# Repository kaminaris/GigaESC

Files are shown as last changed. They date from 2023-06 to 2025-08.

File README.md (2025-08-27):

# GigaESC - 40s 400A

GigaESC - Based upon the VESC®*-Project VESC is a registered TM, owned by Benjamin Vedder




* Modular design
* Logic board
* Separate Power Stage (Mosfet) board
* 40s capable
* Up to 188V (Mosfets and caps up to 200V)
* Up to 300A (depending on choice of mosfets)
* Hall sensor current measurement or low side shunts
* Built in IMU - LSM6DS3TR-C
* Optional Hardware current protection
* Designed for easy manufacturing at JLCPcb (KiCad Fabrication Toolkit)

Licensed under [Creative Commons Attribution-NonCommercial-ShareAlike 4.0 International License](https://creativecommons.org/licenses/by-nc-sa/4.0/legalcode.en)


# ⚠️Please do not order before contacting me on discord️⚠️

https://discord.gg/embedded

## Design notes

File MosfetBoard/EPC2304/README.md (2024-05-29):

# GigaESC - EPC2304

---

# ⚠️Please do not order before contacting me on discord️⚠️

this is a very hard board to solder requires:

- Good knowledge of microsoldering
- **A microscope**
- Hot air capable of reaching 450°C
- A very thin soldering iron tip
- An oscilloscope

## GaN Soldering procedure

Use 60/40 solder from a reputable source. Trying to use lead-free solder by hand will be extremely difficult. Using poor-quality products will also result in failure, and this applies to flux as well.

This board has 4 layers, so it can absorb a lot of heat. Using high-quality solder is essential because the board is very sensitive to cold joints.

Having a good soldering iron is crucial and can make the difference between success and failure.

To solder GaN mosfets i strongly recommend using soldering paste instead, everything else can be done with wire tin.

1. Apply solder paste with flux on the footprint.
2. Position the GaN mosfet in place.
3. Use hot air until the solder melts and the GaN device is securely in place, applying gentle pressure to ensure proper contact.
4. Remove any excess solder with a soldering iron.
5. Allow the solder to cool down.

**[Repeat]**

1. Heat the solder joint again with hot air.
2. Apply flux.
3. Use tweezers to gently swirl the MOSFET, ensuring each pad has an equal amount of solder.
4. Reposition the MOSFET properly.
5. Allow the solder to cool down.

**[Repeat until the GaN mosfet self-aligns perfectly.]**

**⚠️While doing soldering procedure, make sure there are no microblobs of solder underneath mosfets.**
This may take a couple of tries to get it right.

## Testing procedure

1. Check with a multimeter the following parameters:
    - Resistance between + and - terminals: Should be very high, nearly open loop.
    - Resistance between each phase to ground: Should be greater than 40 kOhms.
    - Resistance between each phase to VBat+: Should be in the megaohms range.
    - Phase comparison: Each phase should have similar resistance readings to the others.
    - Gate connection check: Ensure each gate connects to the main PL and PH lines (this can be verified from the top of the PCB).
2. If electrically everything seems fine, connect to the main board and turn on the VESC:
    - Error code check: If any error code appears, there may be an issue, most commonly cold joints.
    - Current offset measurement:
        - Measure current offsets before doing anything with the VESC. 
        - They should all be within +/-10 LSB and around 2070
         
3. Connect the motor and measure its RL properties:
    - If you observe any abnormal values, such as very high inductance:
       - Check and fix any cold joints.
       - Use a multimeter to ensure each current sensor at idle is outputting about 1.65V.
       - Ensure each current sensor is receiving 5V.
4. Once any initial problems are resolved:
    - Set the current to the lowest possible value in FOC -> General and perform a full detection until all parameters are green and appear reasonable:
    
    - If you have another VESC, compare results with it. It will depend on motor itself so do not compare them to mine.
    - Perform a short double pulse test, for example: double_pulse 100 10 5 10. Confirm both edges look okay and are not overshooting.
    - Perform the motor detection.

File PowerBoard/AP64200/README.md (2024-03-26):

# Power Supply AP64200

## ⚠ Not working - Do not use ⚠

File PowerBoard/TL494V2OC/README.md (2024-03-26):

# Power Supply TL494 V2

Version without power switch

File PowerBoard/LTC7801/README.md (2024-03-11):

# Power Supply LTC7801

## ⚠ Not working - Do not use ⚠

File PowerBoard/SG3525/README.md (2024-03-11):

# Power Supply SG3525

## ⚠ Not working - Do not use ⚠

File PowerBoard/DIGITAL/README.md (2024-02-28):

# Power Supply DIGITAL

## ⚠ Not working - Do not use ⚠

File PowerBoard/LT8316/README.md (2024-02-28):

# Power Supply LT8316

## ⚠ Not working - Do not use ⚠

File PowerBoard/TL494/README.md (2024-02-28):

# Power Supply TL494

Version without power switch

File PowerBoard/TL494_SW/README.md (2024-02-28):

# Power Supply TL494

Version with power switch

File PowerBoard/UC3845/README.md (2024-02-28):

# Power Supply UC3845

## ⚠ Not working - Do not use ⚠

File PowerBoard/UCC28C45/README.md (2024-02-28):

# Power Supply UCC28C45

## ⚠ Not working - Do not use ⚠

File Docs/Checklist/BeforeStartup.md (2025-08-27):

# Things to check before starting up VESC for first time

1. Visual inspection for solder bridges and correct orientation of polarized parts.
2. Check for shorts between power rails:
   - battery + and -
   - motor phases
   - 12V, 5V, and 3.3V rails
3. Check if all drivers capacitors have roughly the same voltage drop.
4. Use a current-limited power supply for initial power-up 1-3A should be enough.

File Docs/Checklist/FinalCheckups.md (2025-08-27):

# Final Checkups for VESC-based ESC

2. Use a thermal camera to check for unexpected hot spots during operation at low power.
3. Verify deadtime settings in firmware/configuration to prevent shoot-through:
    - Connect oscilloscope to high and low gates. Make sure the deadtime is sufficient to prevent overlap.
      
    - Make sure phase voltage does not spike too much
      
4. Double pulse test:
    - Clean the board and ensure no debris or solder balls are present.
    - Connect one probe to phase 1 and another to output of current sensor.
    - `double_pulse 100 10 5 10` - Preface, first on time, off time, second on time
    - gradually increase the voltage and time on for the first pulse looking out for issues
    - Check for double pulses on the high side gate.
      
6. Run foc_openloop_test to verify motor operation:
    - Set the test to a low current (e.g., 5A) and observe motor behavior.
    - Ensure the motor spins smoothly without excessive noise or vibration.
    - Check for any abnormal current spikes or temperature increases.
4. Calibrate current sensors using VESC Tool or relevant software, confirm accurate readings.
7. Review all configuration parameters before full-power operation.

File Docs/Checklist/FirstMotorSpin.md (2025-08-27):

# First Motor Spin Checklist for VESC-based ESC

1. **Use bench power supply with current limit (1-3A).** Confirm board powers up without faults.
2. Connect motor phases to ESC
3. Connect to VESC Tool.
4. Set current limits to low values (e.g., 5-10A) in Motor -> General -> Current Tab.
5. Write motor configuration to ESC.
6. Perform motor detection, make sure it ends up with reasonable values.

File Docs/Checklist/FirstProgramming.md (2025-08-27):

# First Programming Checklist for VESC-based ESC

1. Confirm essential power rails 3.3V are present and stable.
2. Connect the programming header SWD to the microcontroller.
3. Ensure the board is powered via a current-limited supply (1-3A max).
4. Use either black magic probe or ST-Link for programming.
5. Load the appropriate firmware onto the ESC.
6. Connect the ESC to a computer via USB and connect with vesc tool.
7. **DO NOT forget to upload bootloader first if it is not already present.**
8. Monitor for excessive current draw or heating during programming. 
It should be around 0.04A

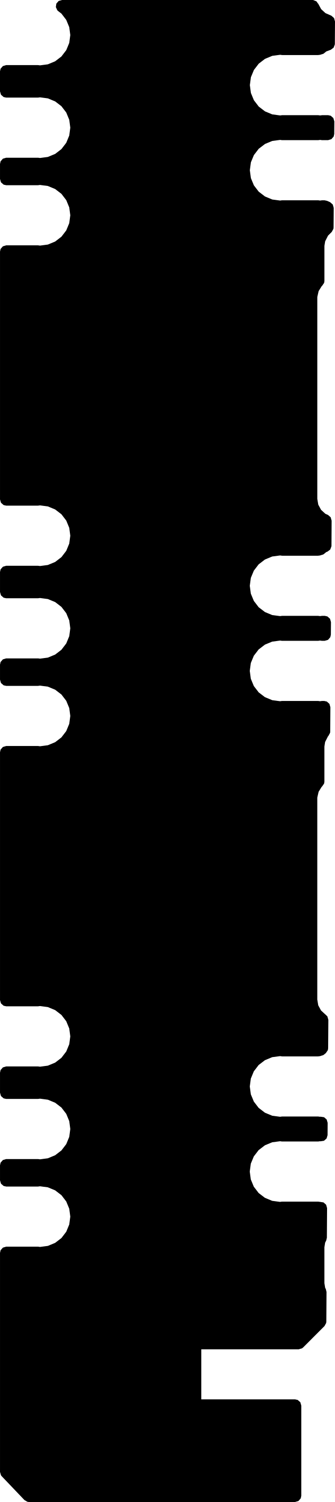
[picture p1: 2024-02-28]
MosfetBoard/EPC2304/bitmap.png

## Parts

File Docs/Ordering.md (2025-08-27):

## Ordering guide

Make sure you have KiCad 7 installed and plugin for kicad "Fabrication Toolkit"

1. Open project you want to edit in Kicad7
2. Open board file (pcbnew)
3. Click the button to export production files



4. New folder will open up with all the files required for jlcpcb
5. Upload gerber.zip on front page
6. Check assembly on the bottom of page, change quantity to 2 (you cannot order just one)



7. Most of the board are top side only with exclusion of power boards.
8. On next page upload appropriate files



9. On next page you will have the opportunity to not place certain components if
   you wish to for example not have certain connectors reducing price of assembly.
   **Each project may have specific assembly guide**
10. Inspect the board on 3d render to make sure all components are placed correctly
11. Proceed to order as usual

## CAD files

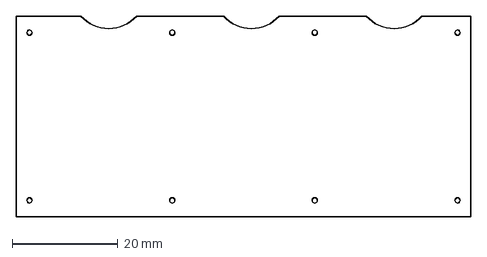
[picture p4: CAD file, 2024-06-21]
3DModels/IHS.dxf
86.0 x 38.0 mm

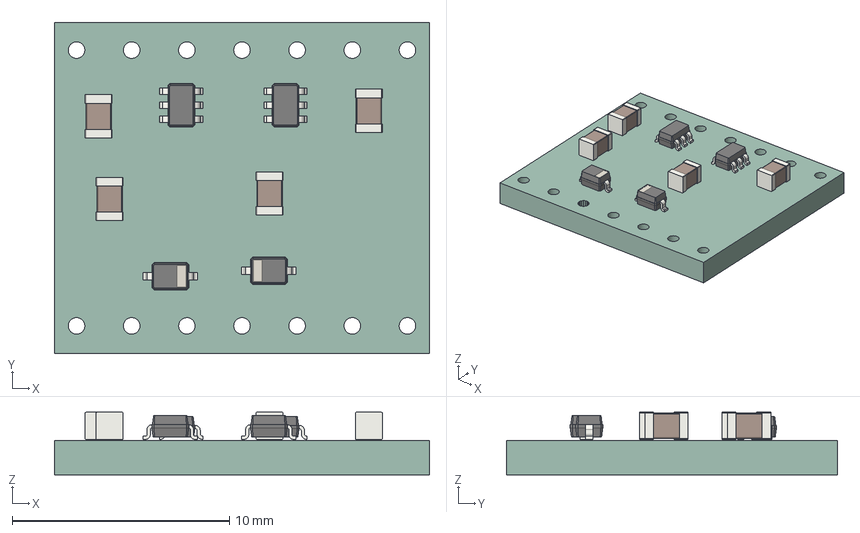
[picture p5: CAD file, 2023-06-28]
HardwareProtection/HardwareProtection.step
17.3 x 15.2 x 2.88 mm
_autosave-HardwareProtection PCB

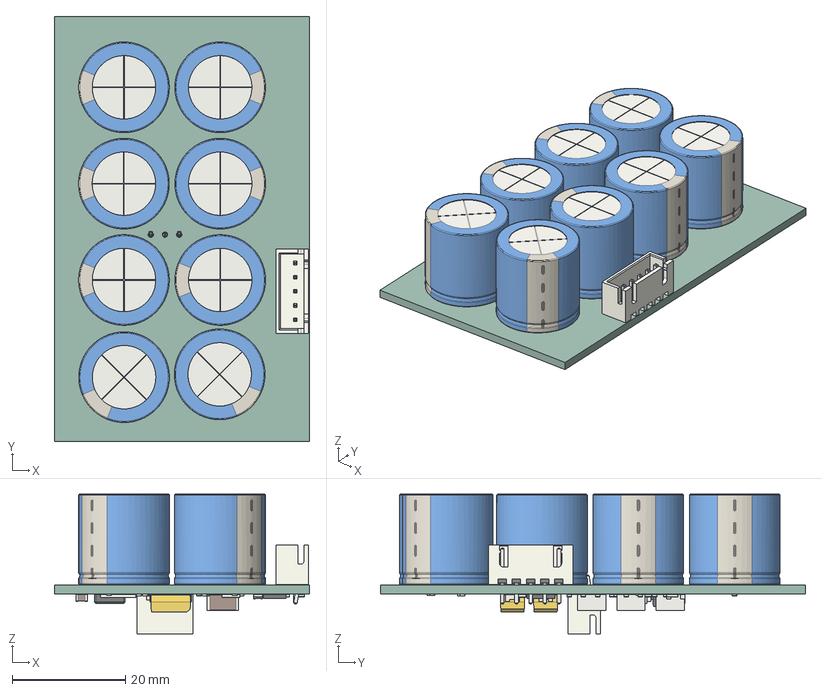
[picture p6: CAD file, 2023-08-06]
PowerBoard/LTC7801/LTC7801.step
45.0 x 75.0 x 24.7 mm
_autosave-LTC7801 PCB

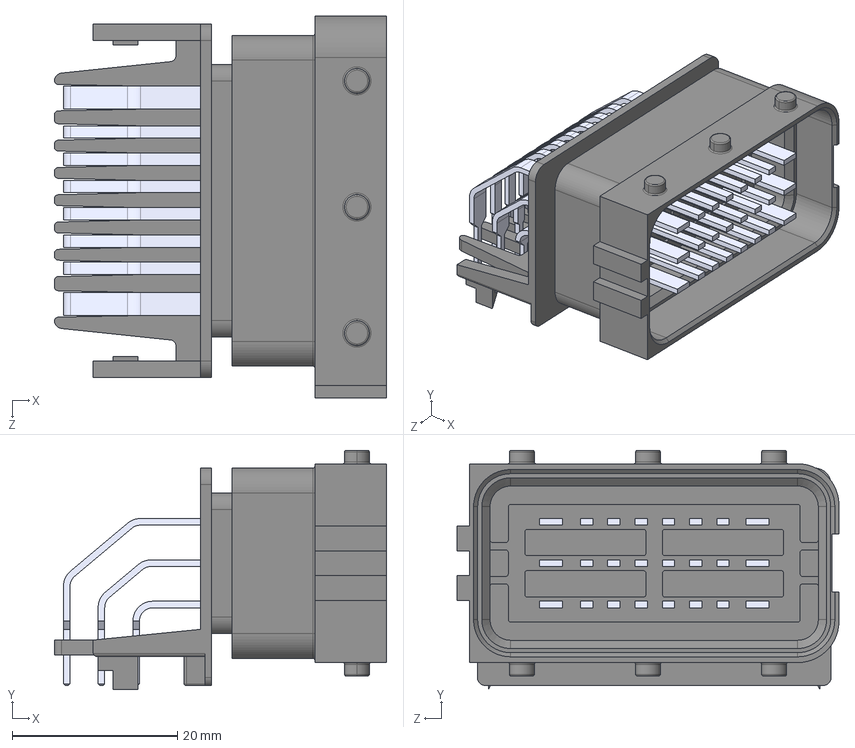
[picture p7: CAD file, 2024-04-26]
Supervisor/3DModels/HCCPHPE24BKA90F.stp
40.2 x 29.0 x 46.2 mm

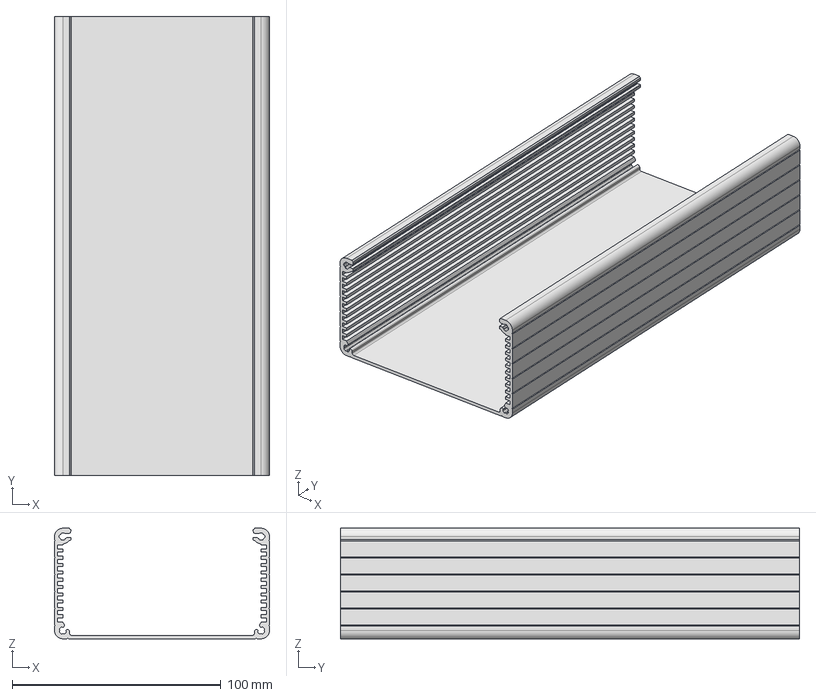
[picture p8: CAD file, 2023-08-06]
WholeDevice/N Extrusion 220mmNoCover.step
103.0 x 220.0 x 53.0 mm

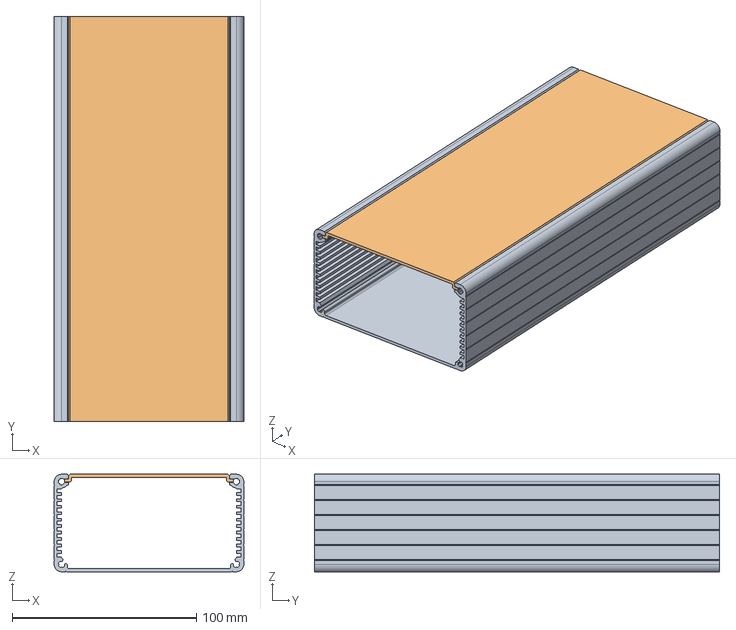
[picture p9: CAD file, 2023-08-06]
WholeDevice/N Extrusion 220mm.stp
103.0 x 220.0 x 53.0 mm
1455N Extrusion 220mm
1455N Cover 220mm

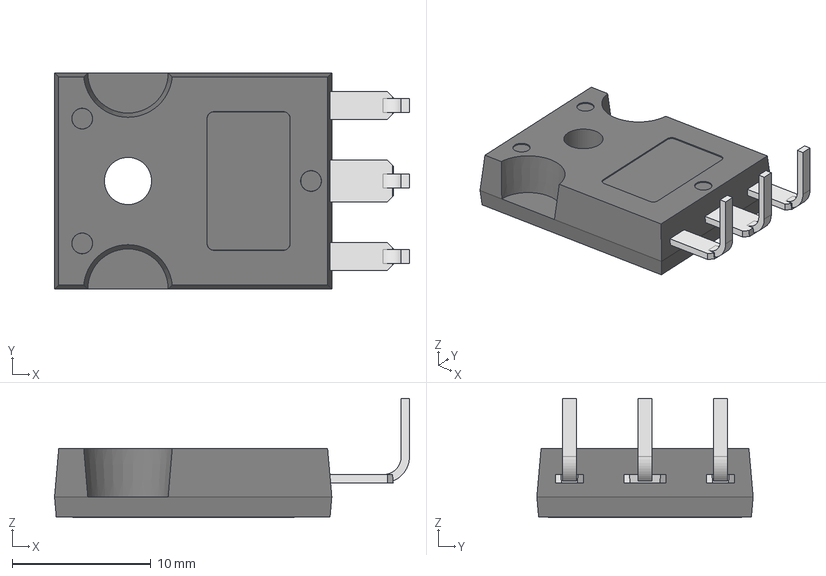
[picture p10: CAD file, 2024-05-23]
3DModels/TO-247_horizontal_back_line.stp
25.6 x 15.6 x 8.60 mm

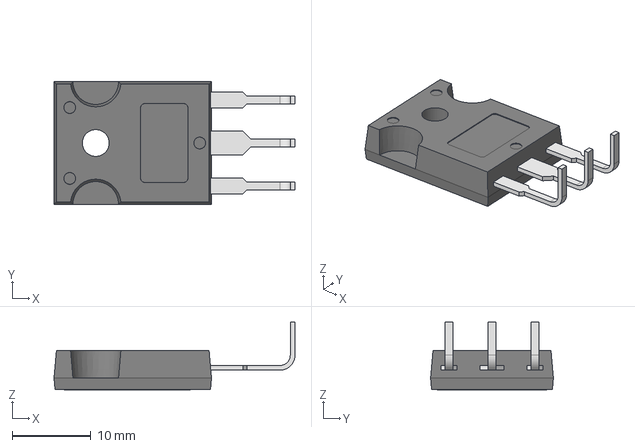
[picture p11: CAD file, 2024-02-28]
3DModels/TO-247_horizontal_back_line-orig.stp
30.6 x 15.6 x 8.60 mm

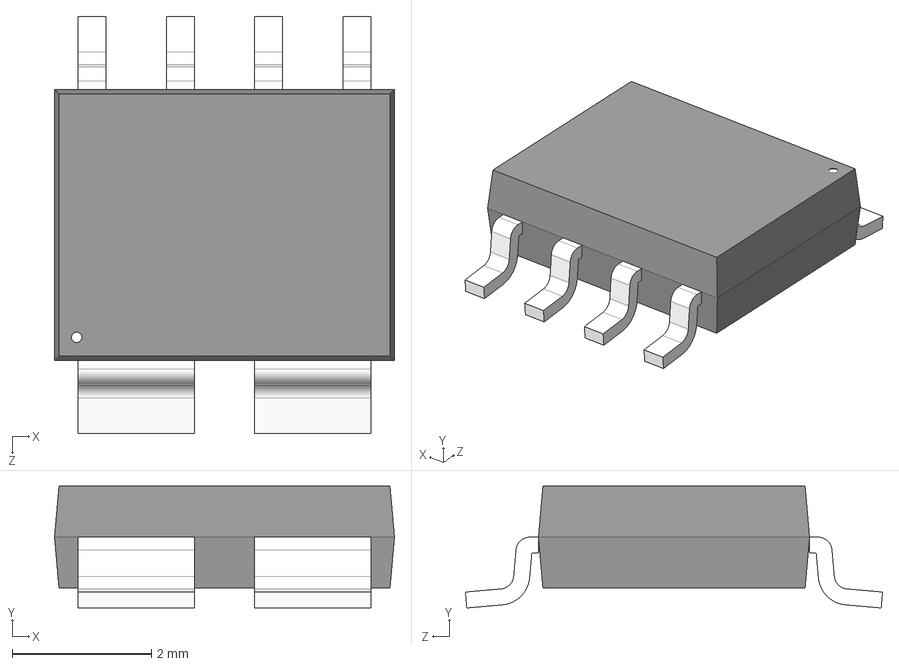
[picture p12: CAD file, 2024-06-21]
3DModels/ACS37030LLZATR-040B3.stp
4.89 x 1.75 x 6.00 mm

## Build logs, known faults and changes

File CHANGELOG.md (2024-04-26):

# Changelog
## V3.3.1
- Supervisor routed
- TL494V2 with over current protection

## V3.3.0
- Updated TL494 V2.1 version
- Initial supervisor

## V3.2.2
- Added TL494 V2 version
- Updated divider resistors with 3-1 ratio.
- Changed JTAG to TagConnect 2030
- Spark switch rework

## V3.2.0
- Moved to KiCad 8
- Updated MCU to bigger package
- Changed inter-board connector to 2x15 pin header
- Added solid mounting screw points
- Updated labels

## V2.1.0
- Added UC3845 power supply board

## V2.0.0
- Connectors changed to JST PH from XH
- Fixed output voltage on ZTP7193Y
- Hardware protection attiny divided for separate digital potentiometers
- Added UART out from attiny for debugging
- Added ESP32-C3 for wireless comm on CANBUS as well as SD card slot for logging
- Added current filter
- Changed analog switches to 7x RS2057XH
- Fixed BRK/Power stage lockout

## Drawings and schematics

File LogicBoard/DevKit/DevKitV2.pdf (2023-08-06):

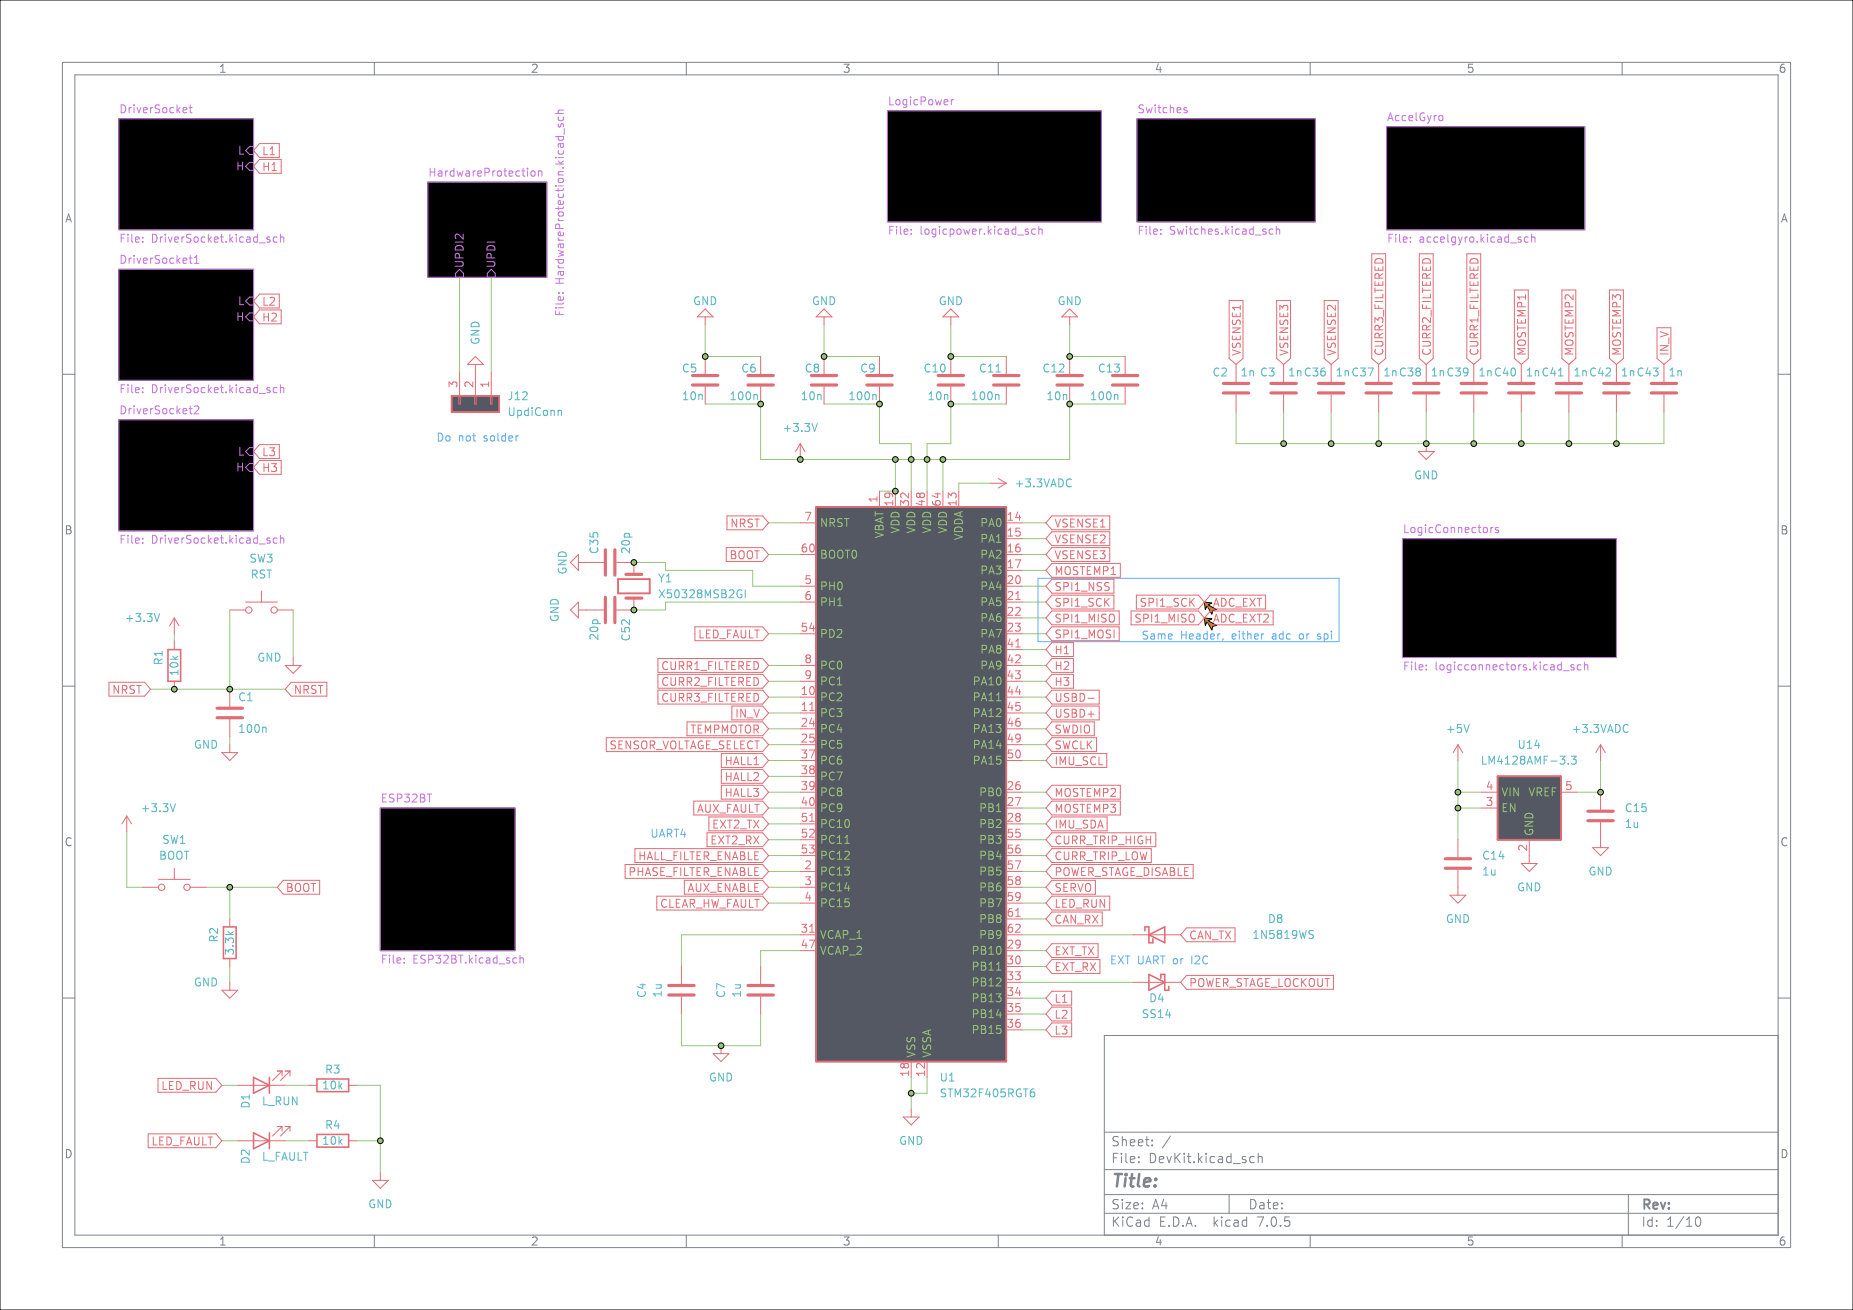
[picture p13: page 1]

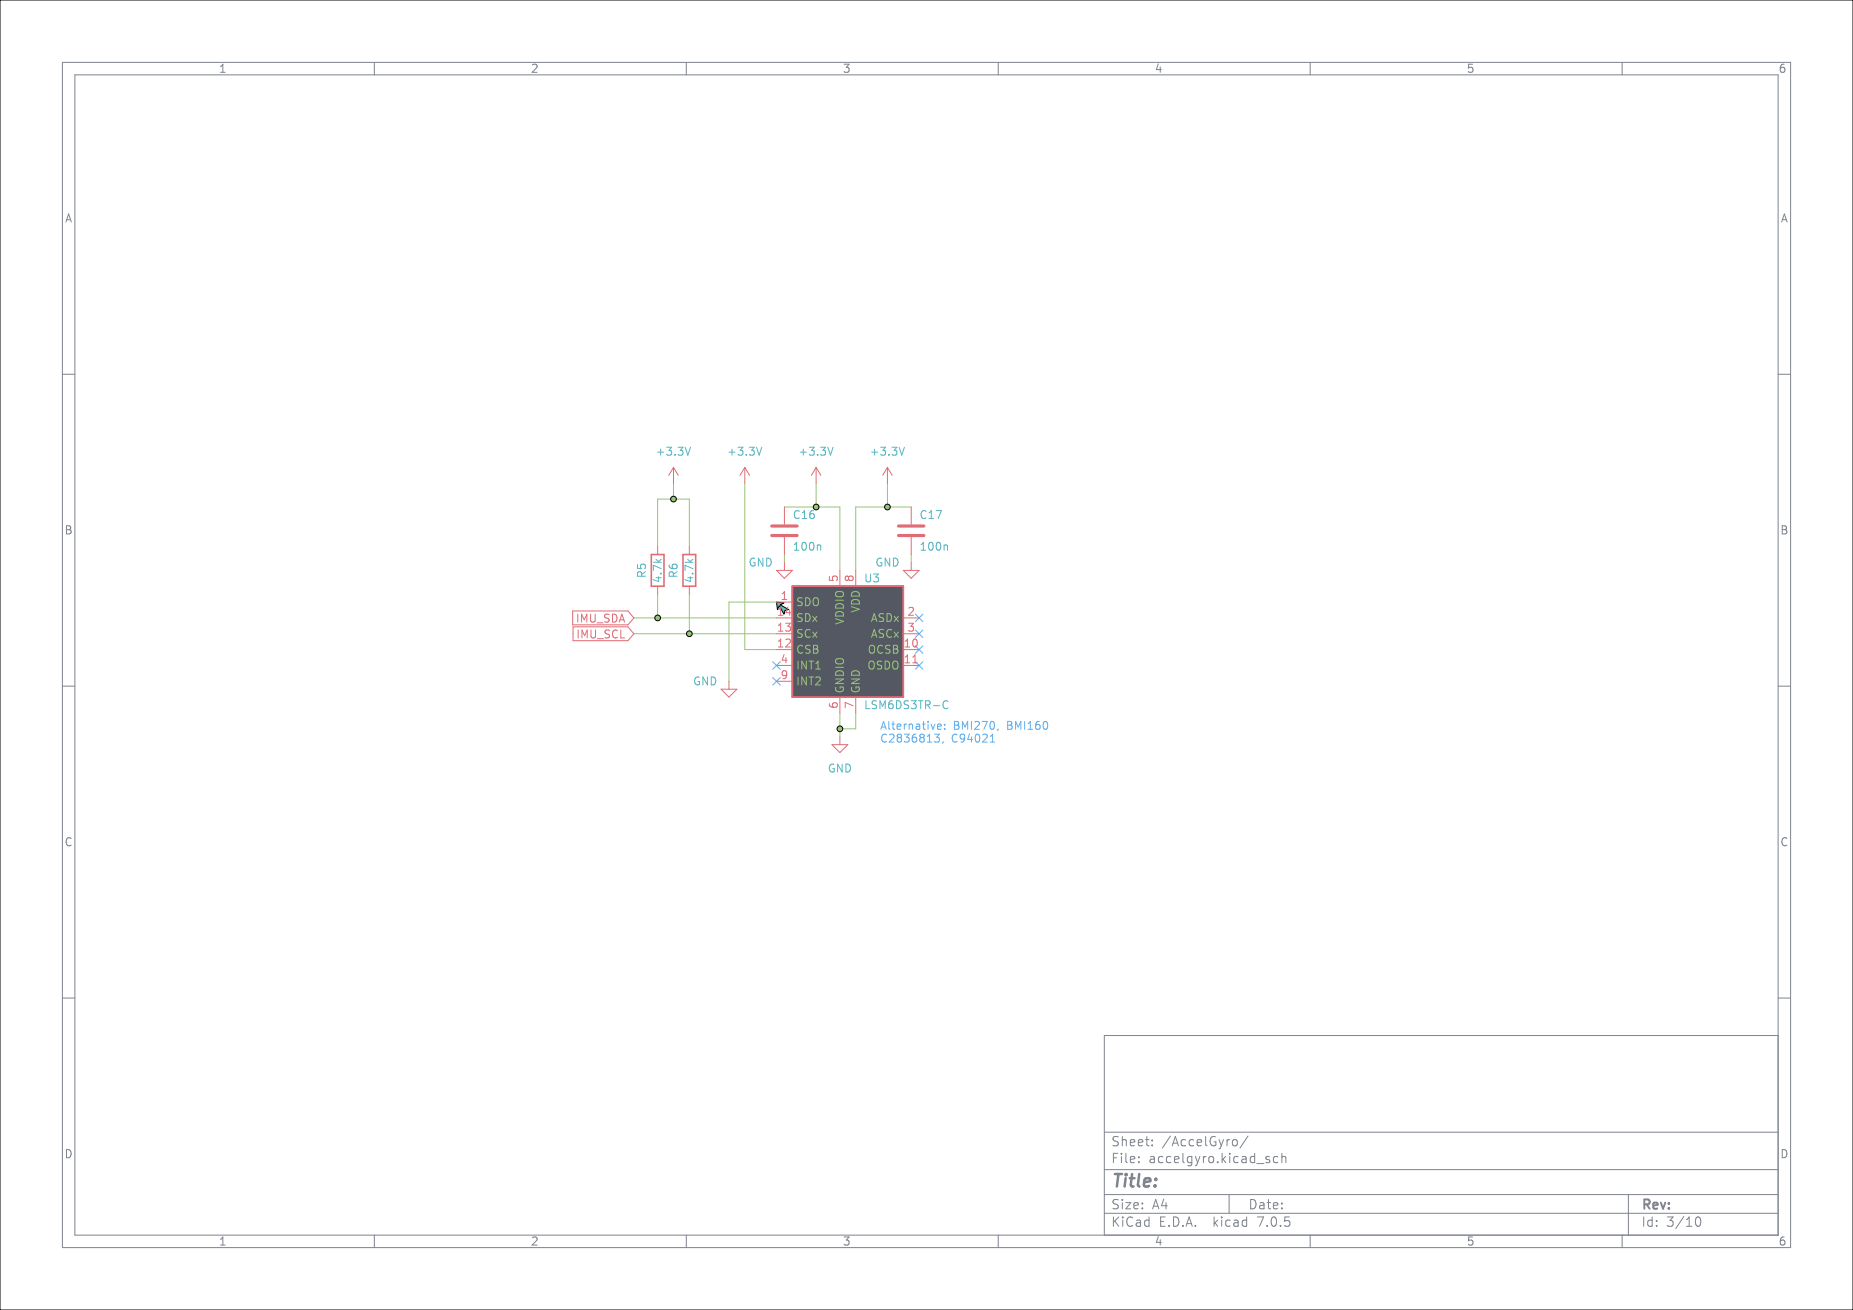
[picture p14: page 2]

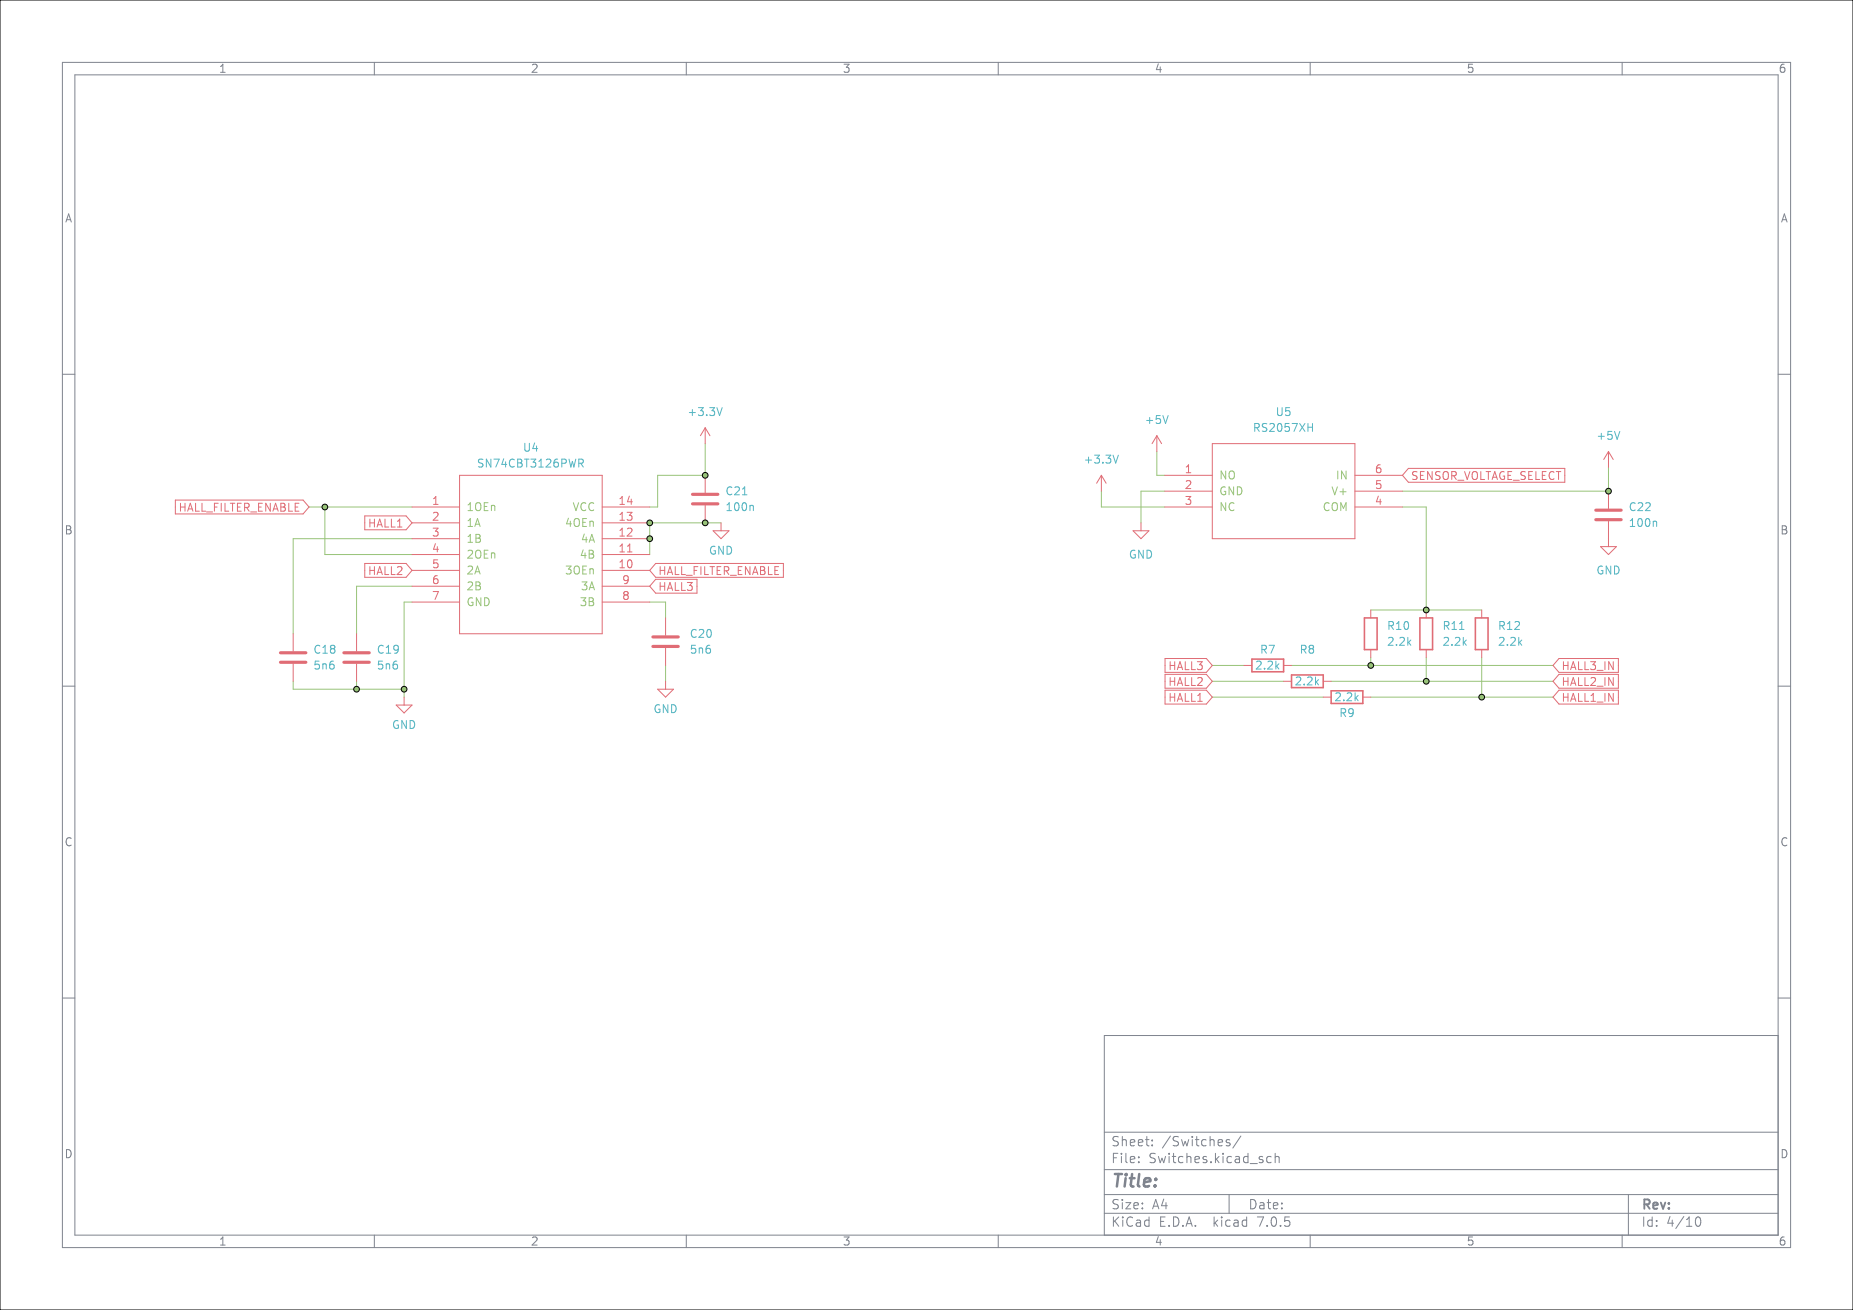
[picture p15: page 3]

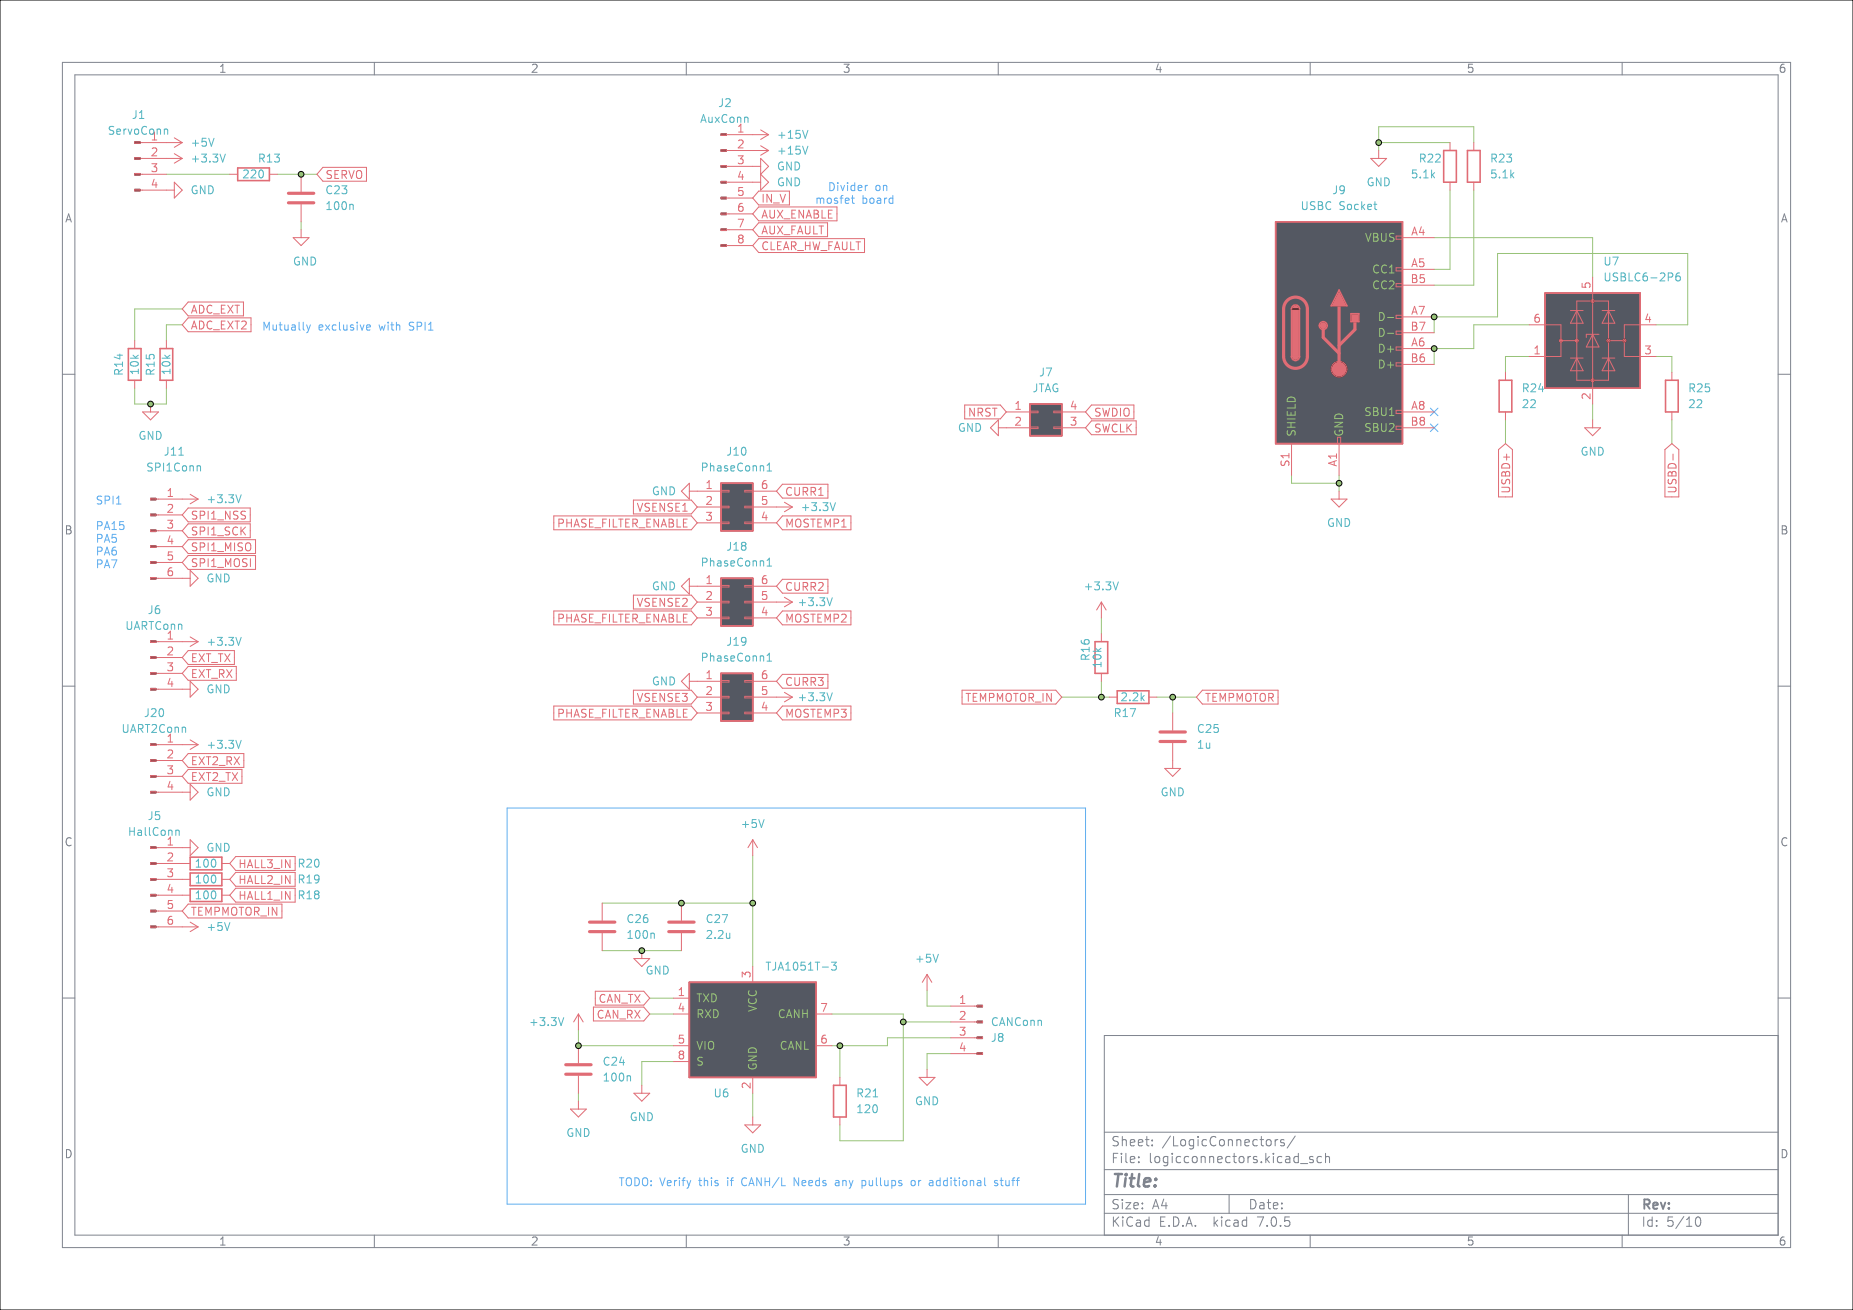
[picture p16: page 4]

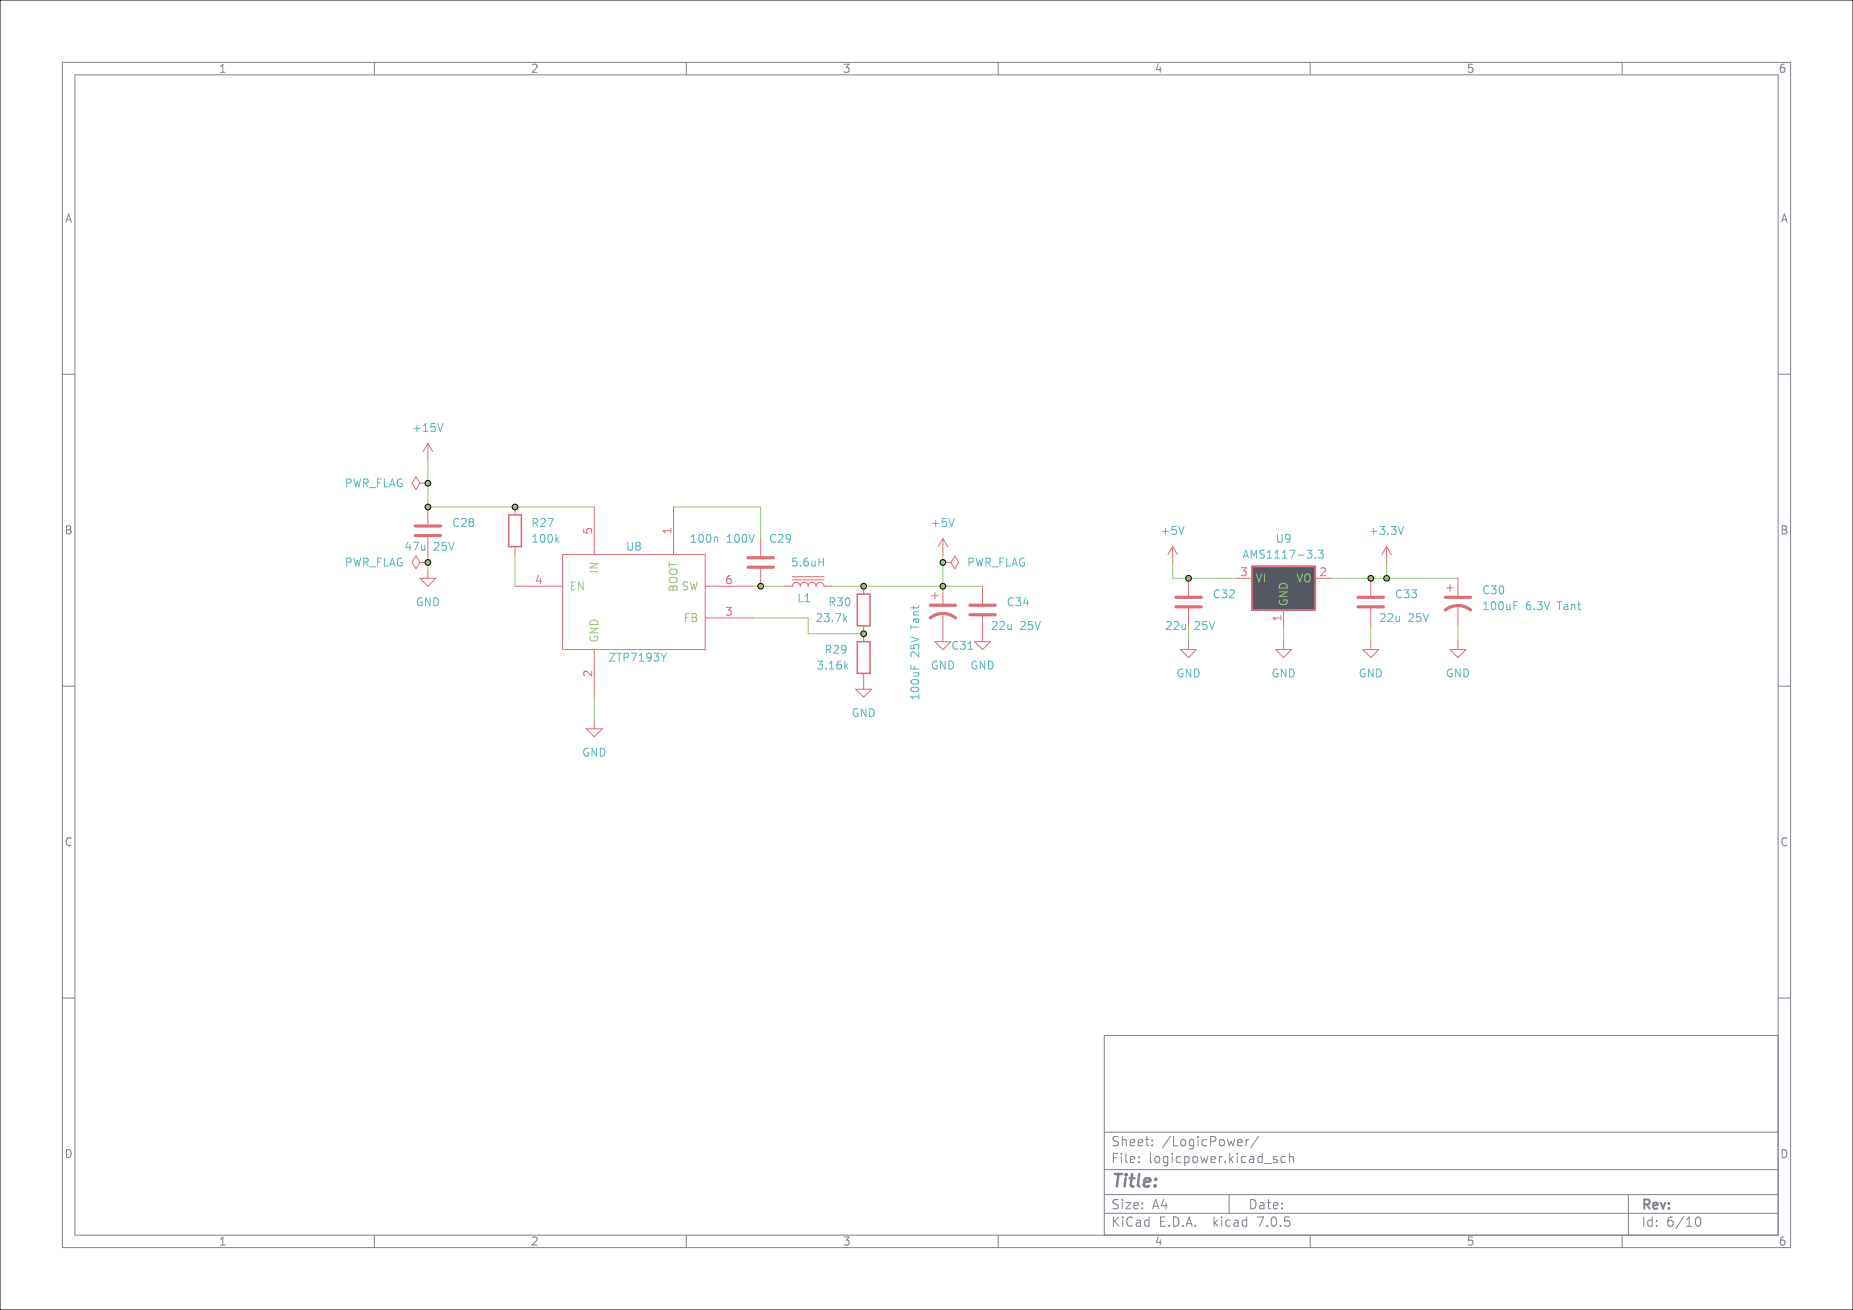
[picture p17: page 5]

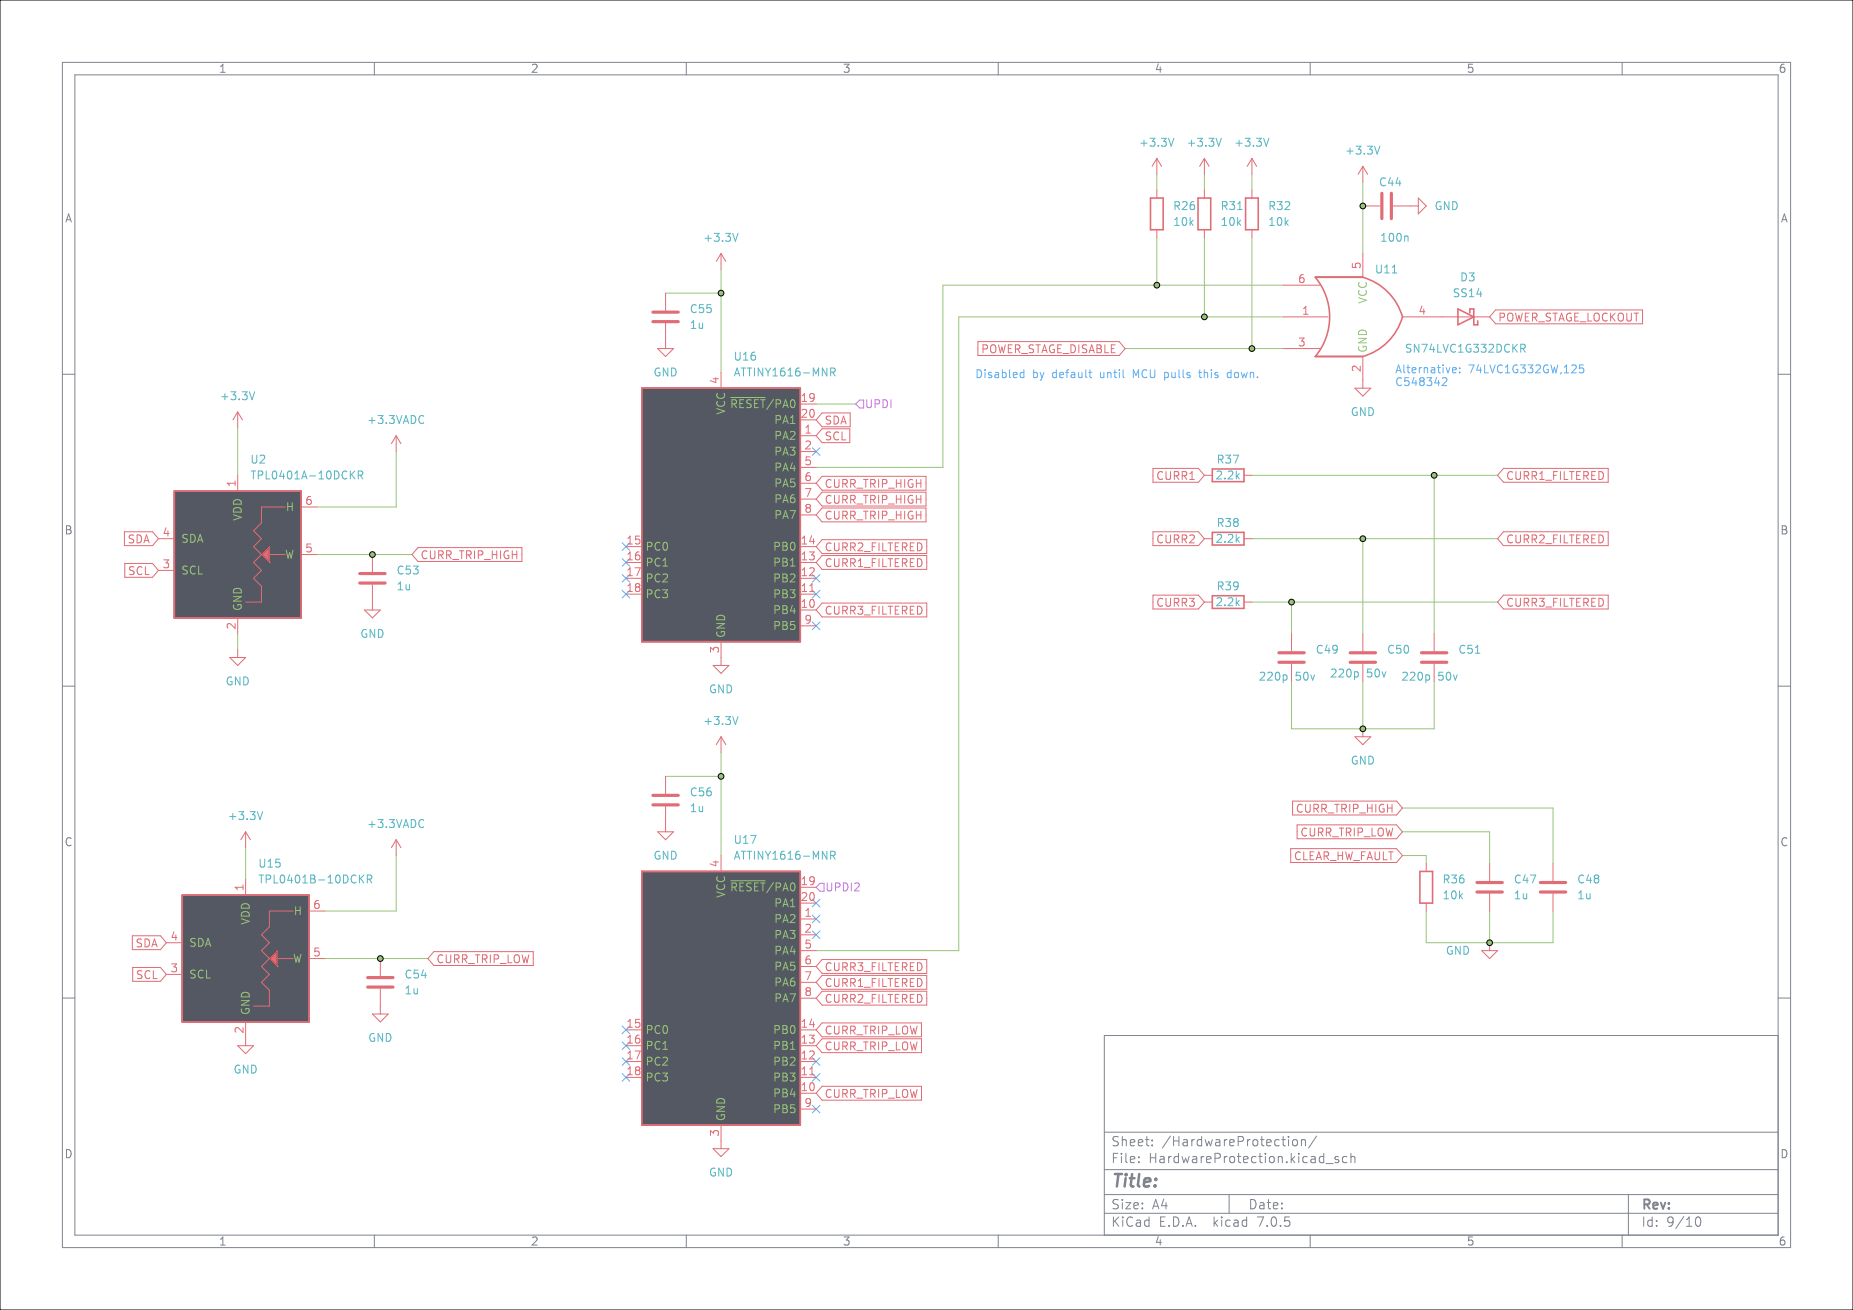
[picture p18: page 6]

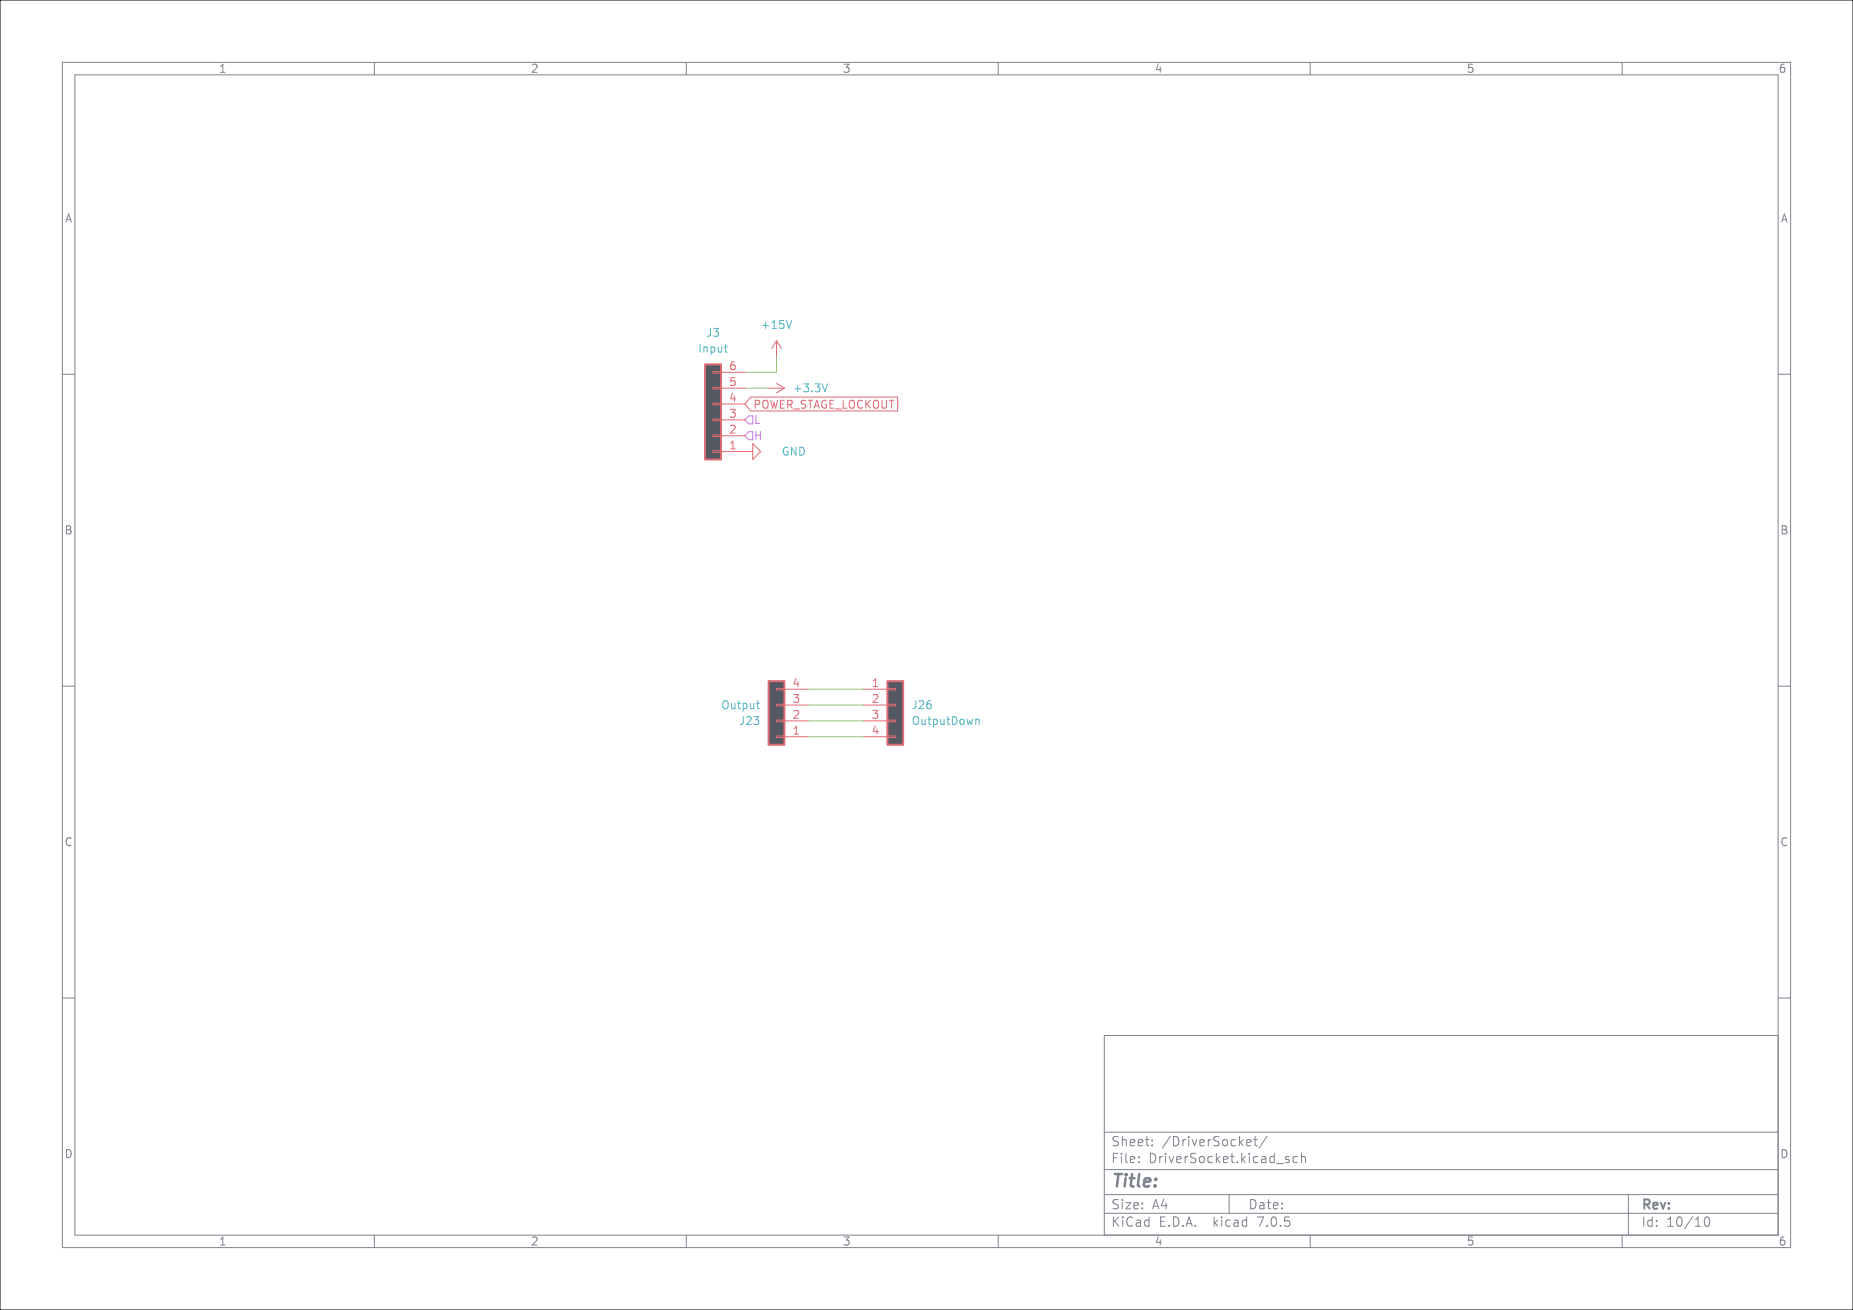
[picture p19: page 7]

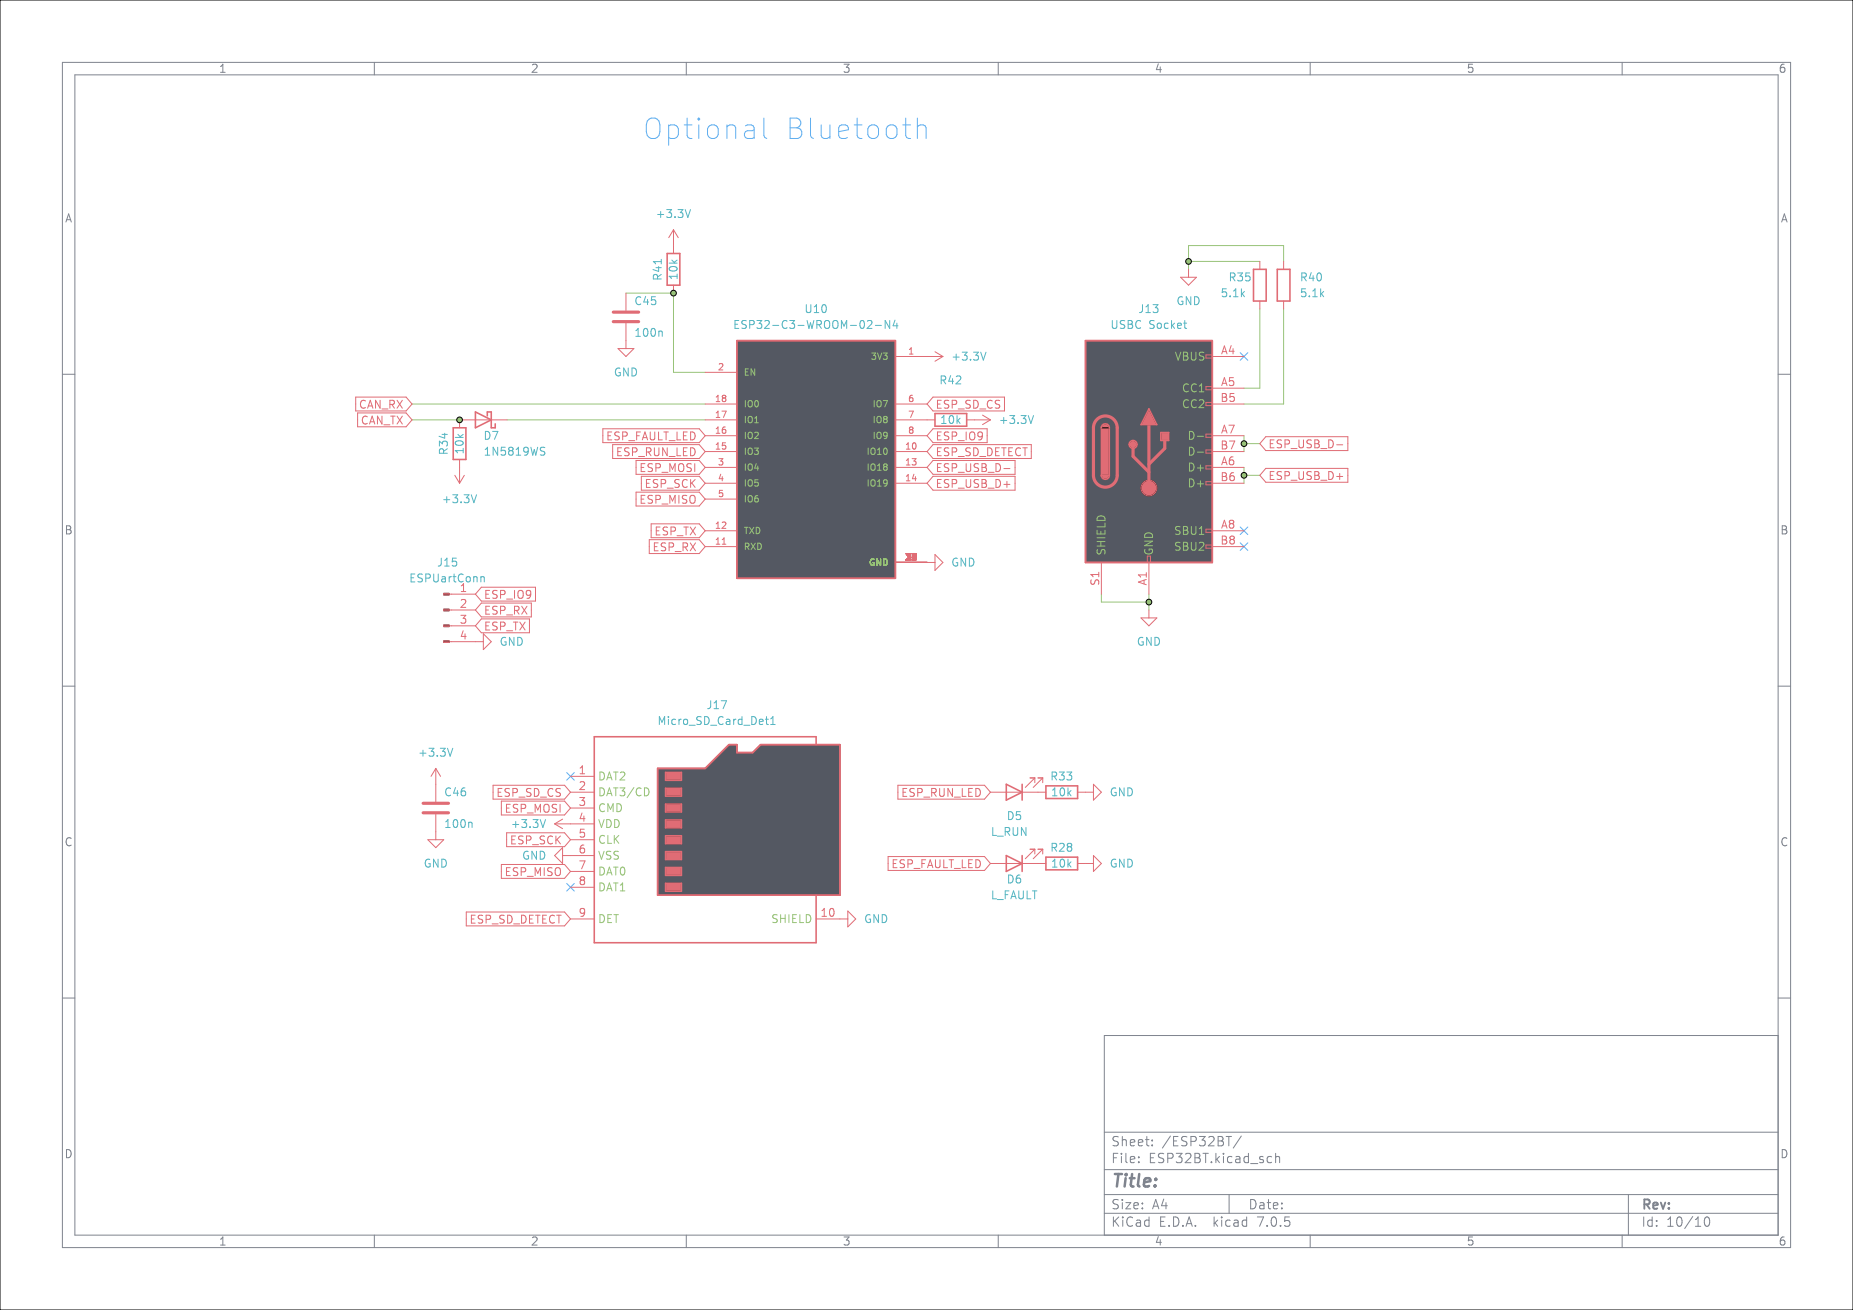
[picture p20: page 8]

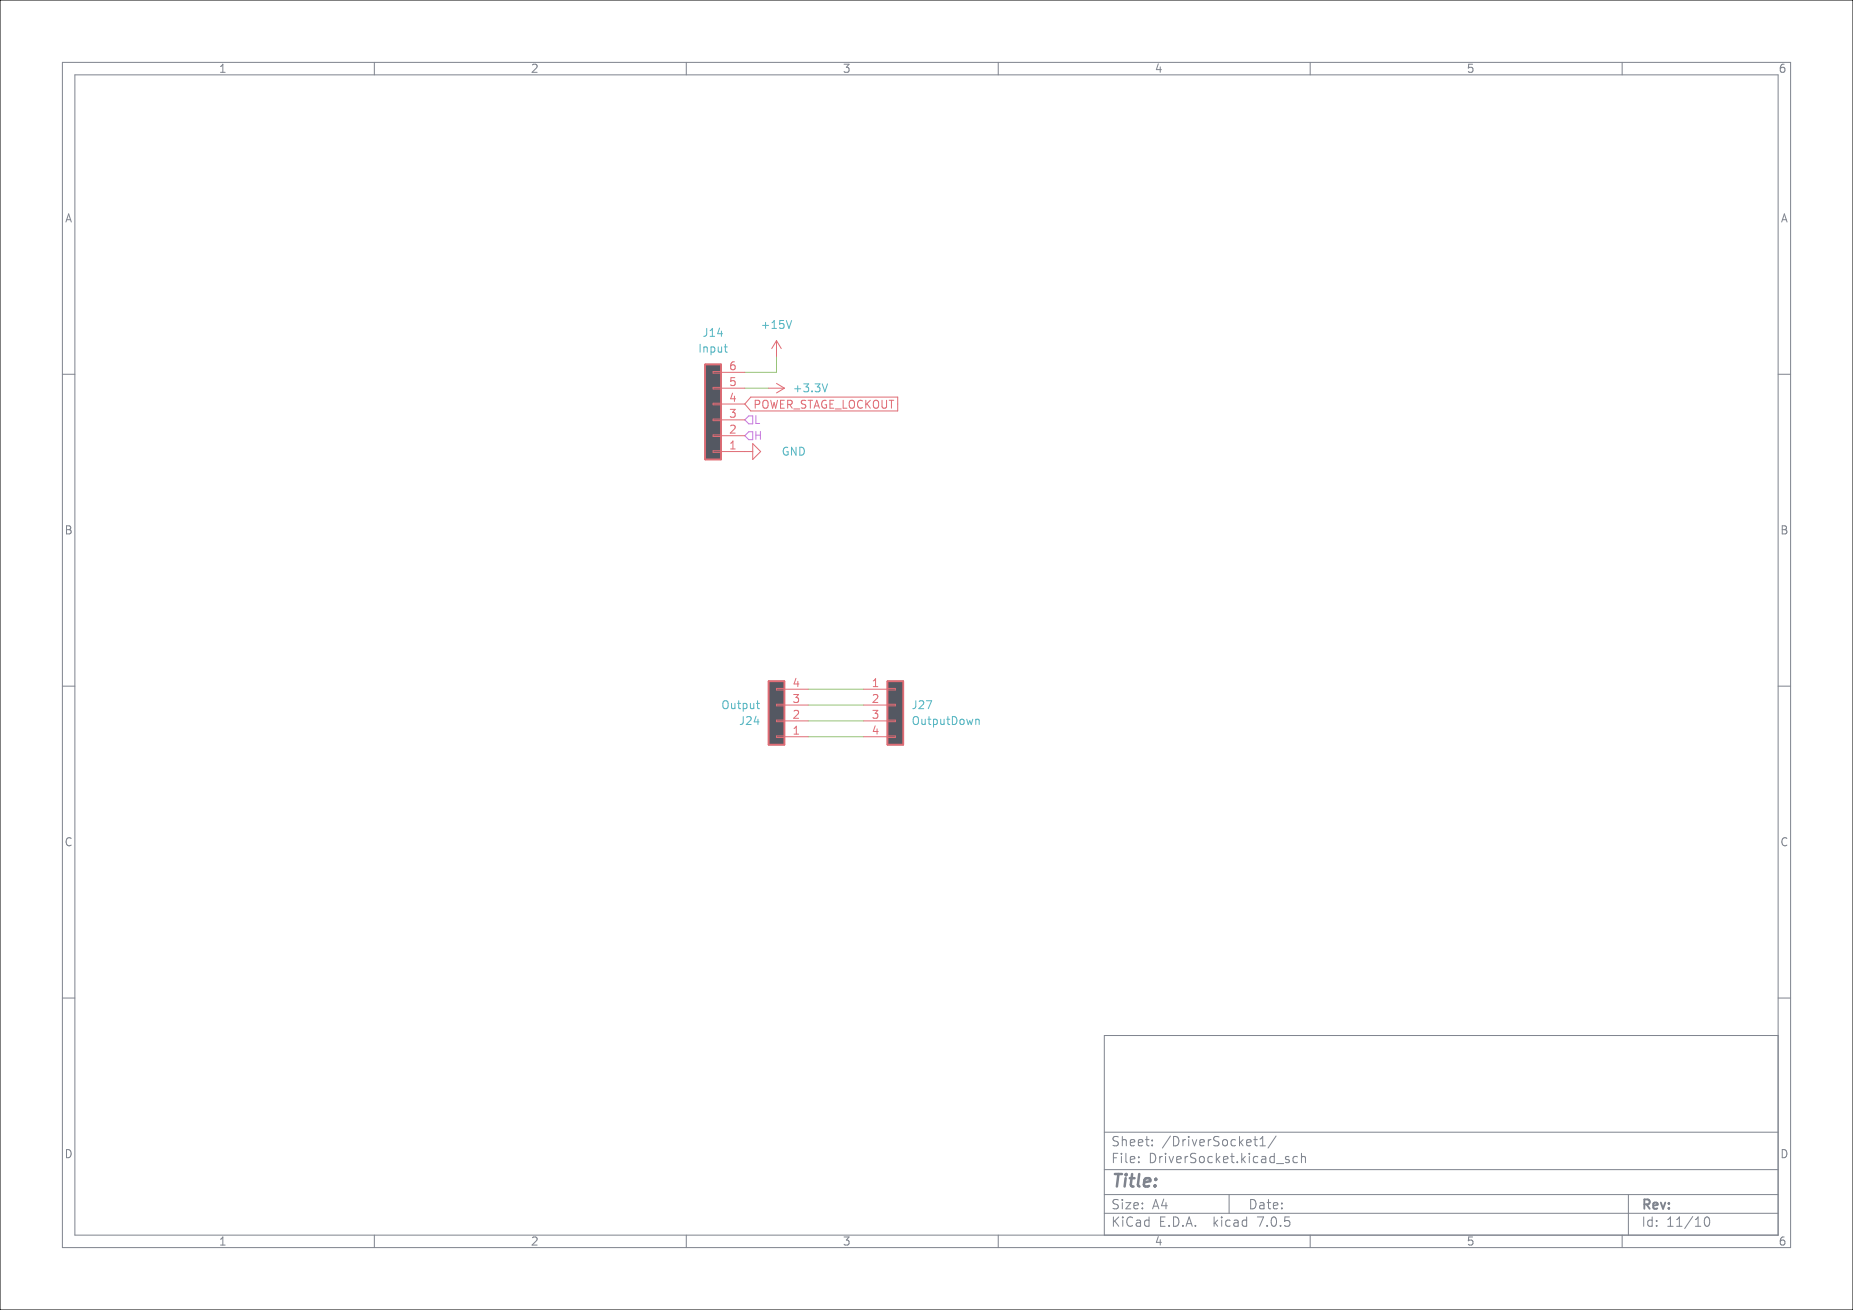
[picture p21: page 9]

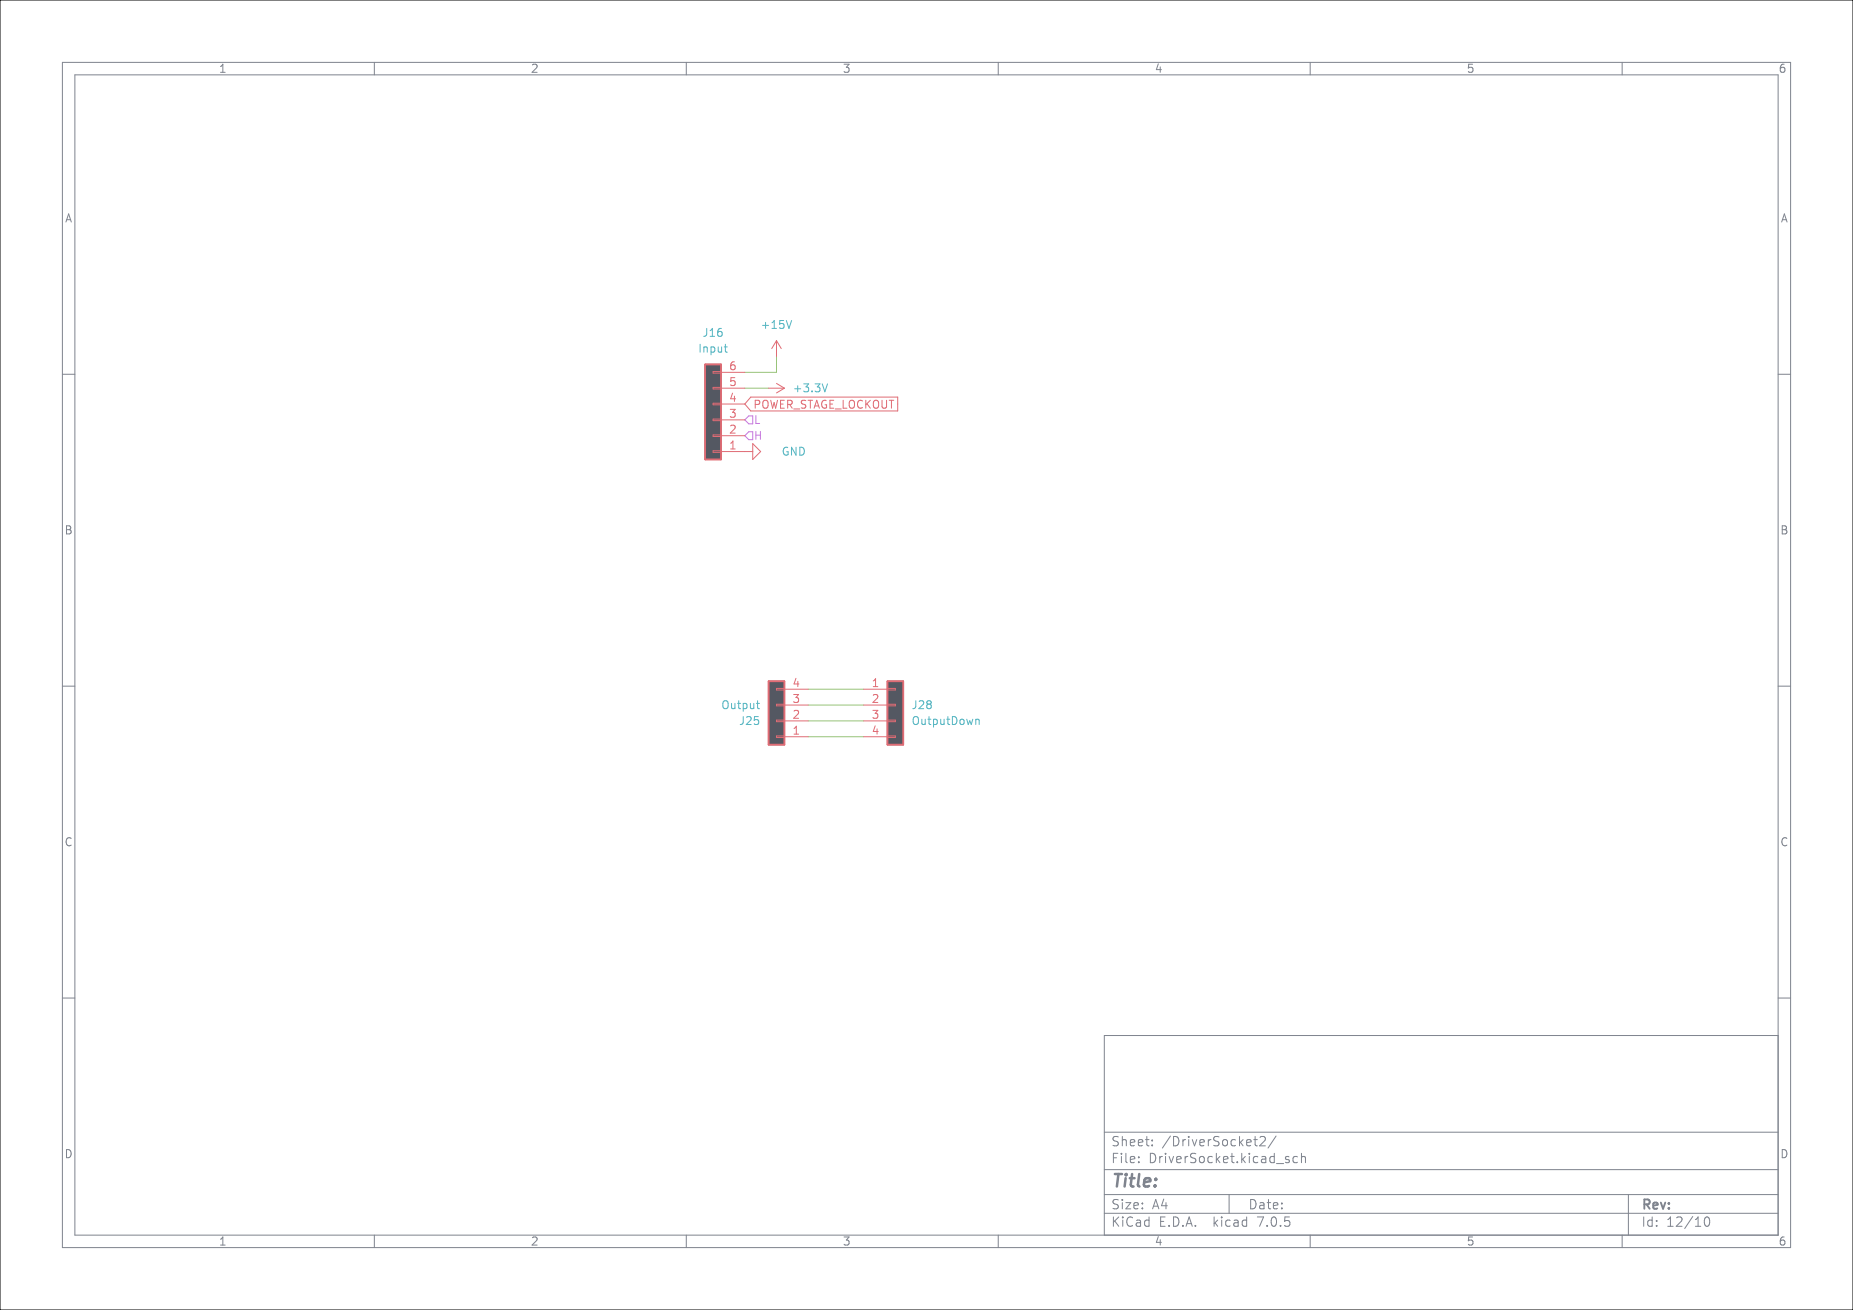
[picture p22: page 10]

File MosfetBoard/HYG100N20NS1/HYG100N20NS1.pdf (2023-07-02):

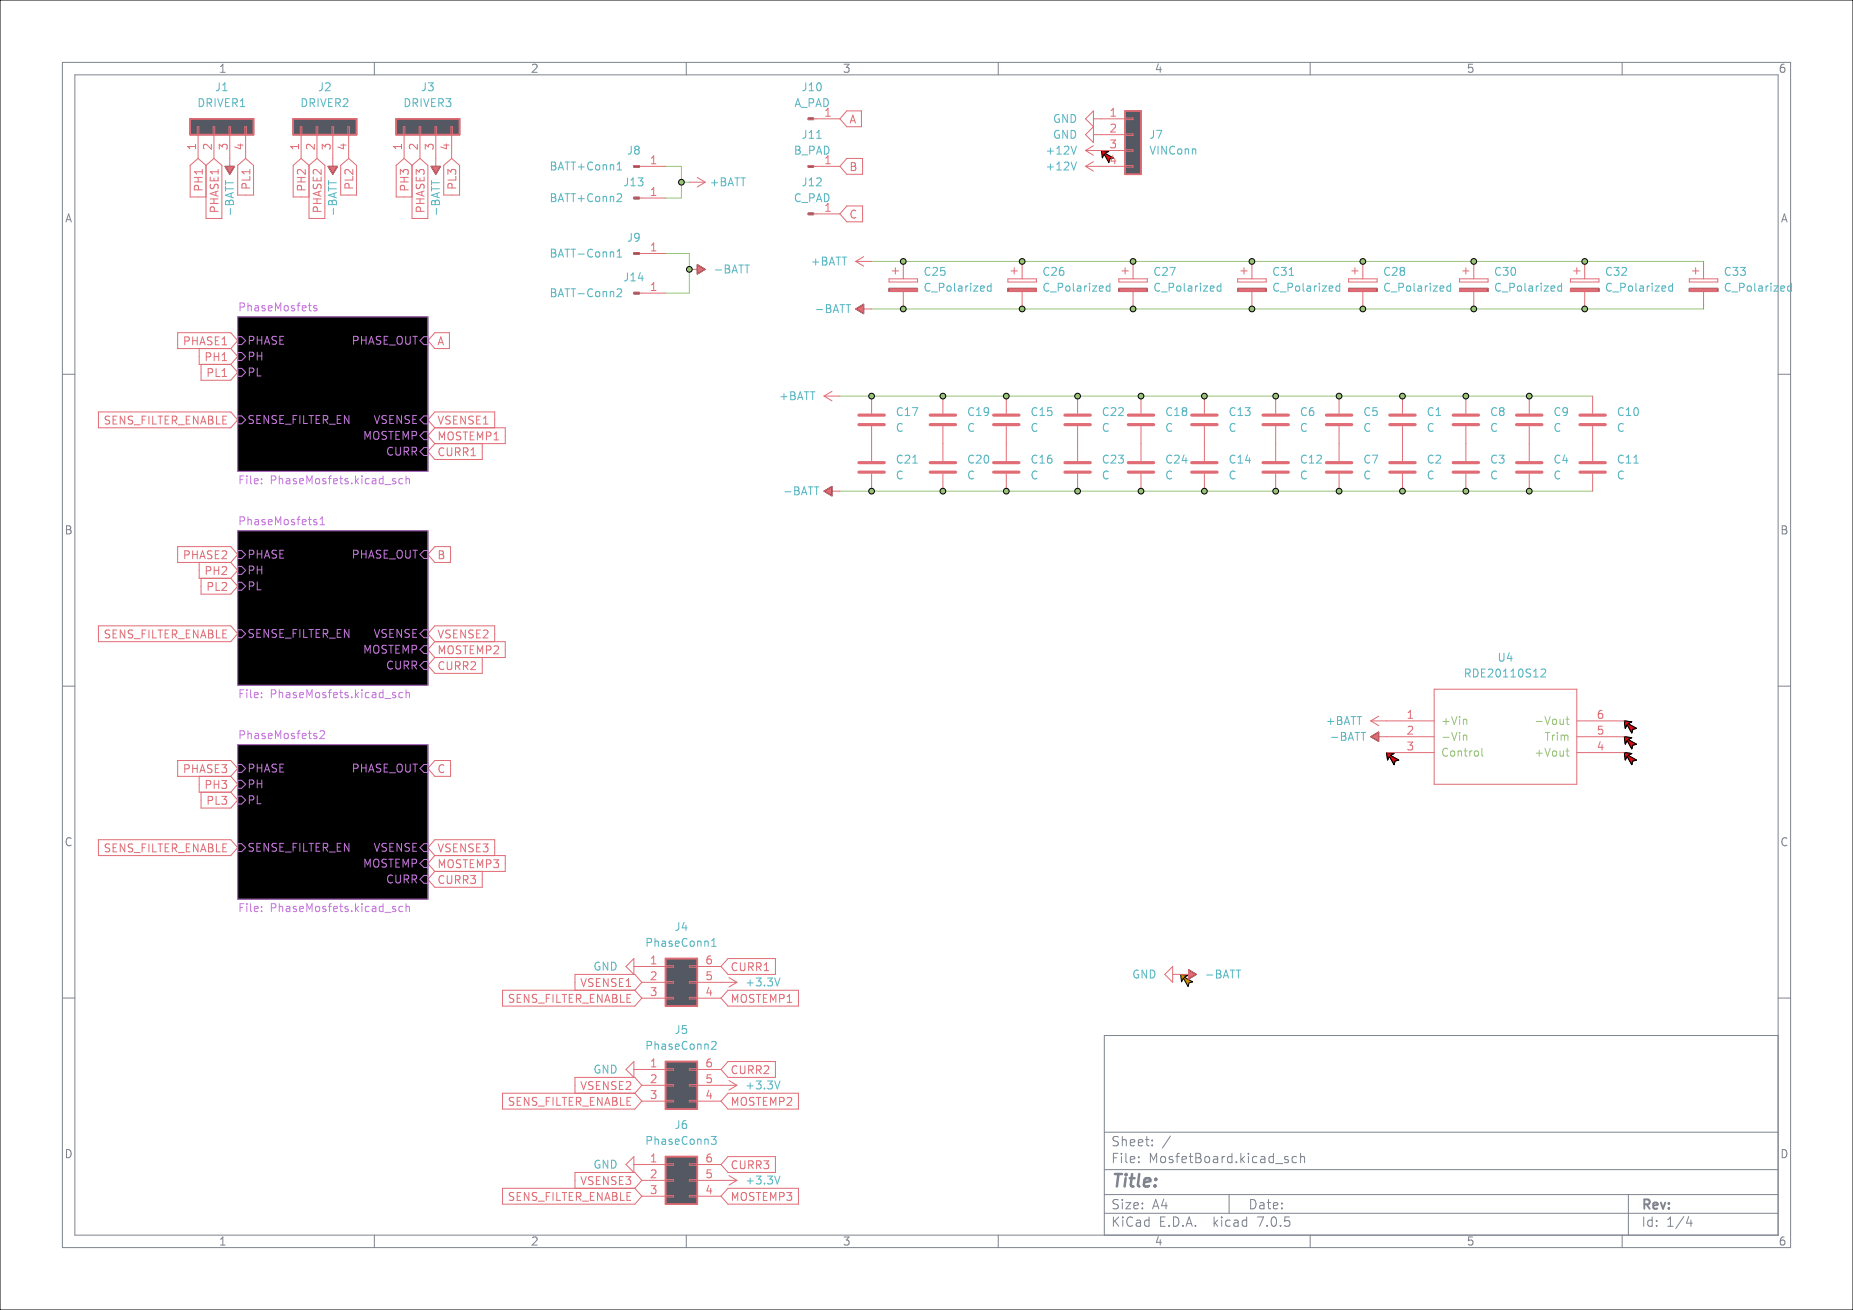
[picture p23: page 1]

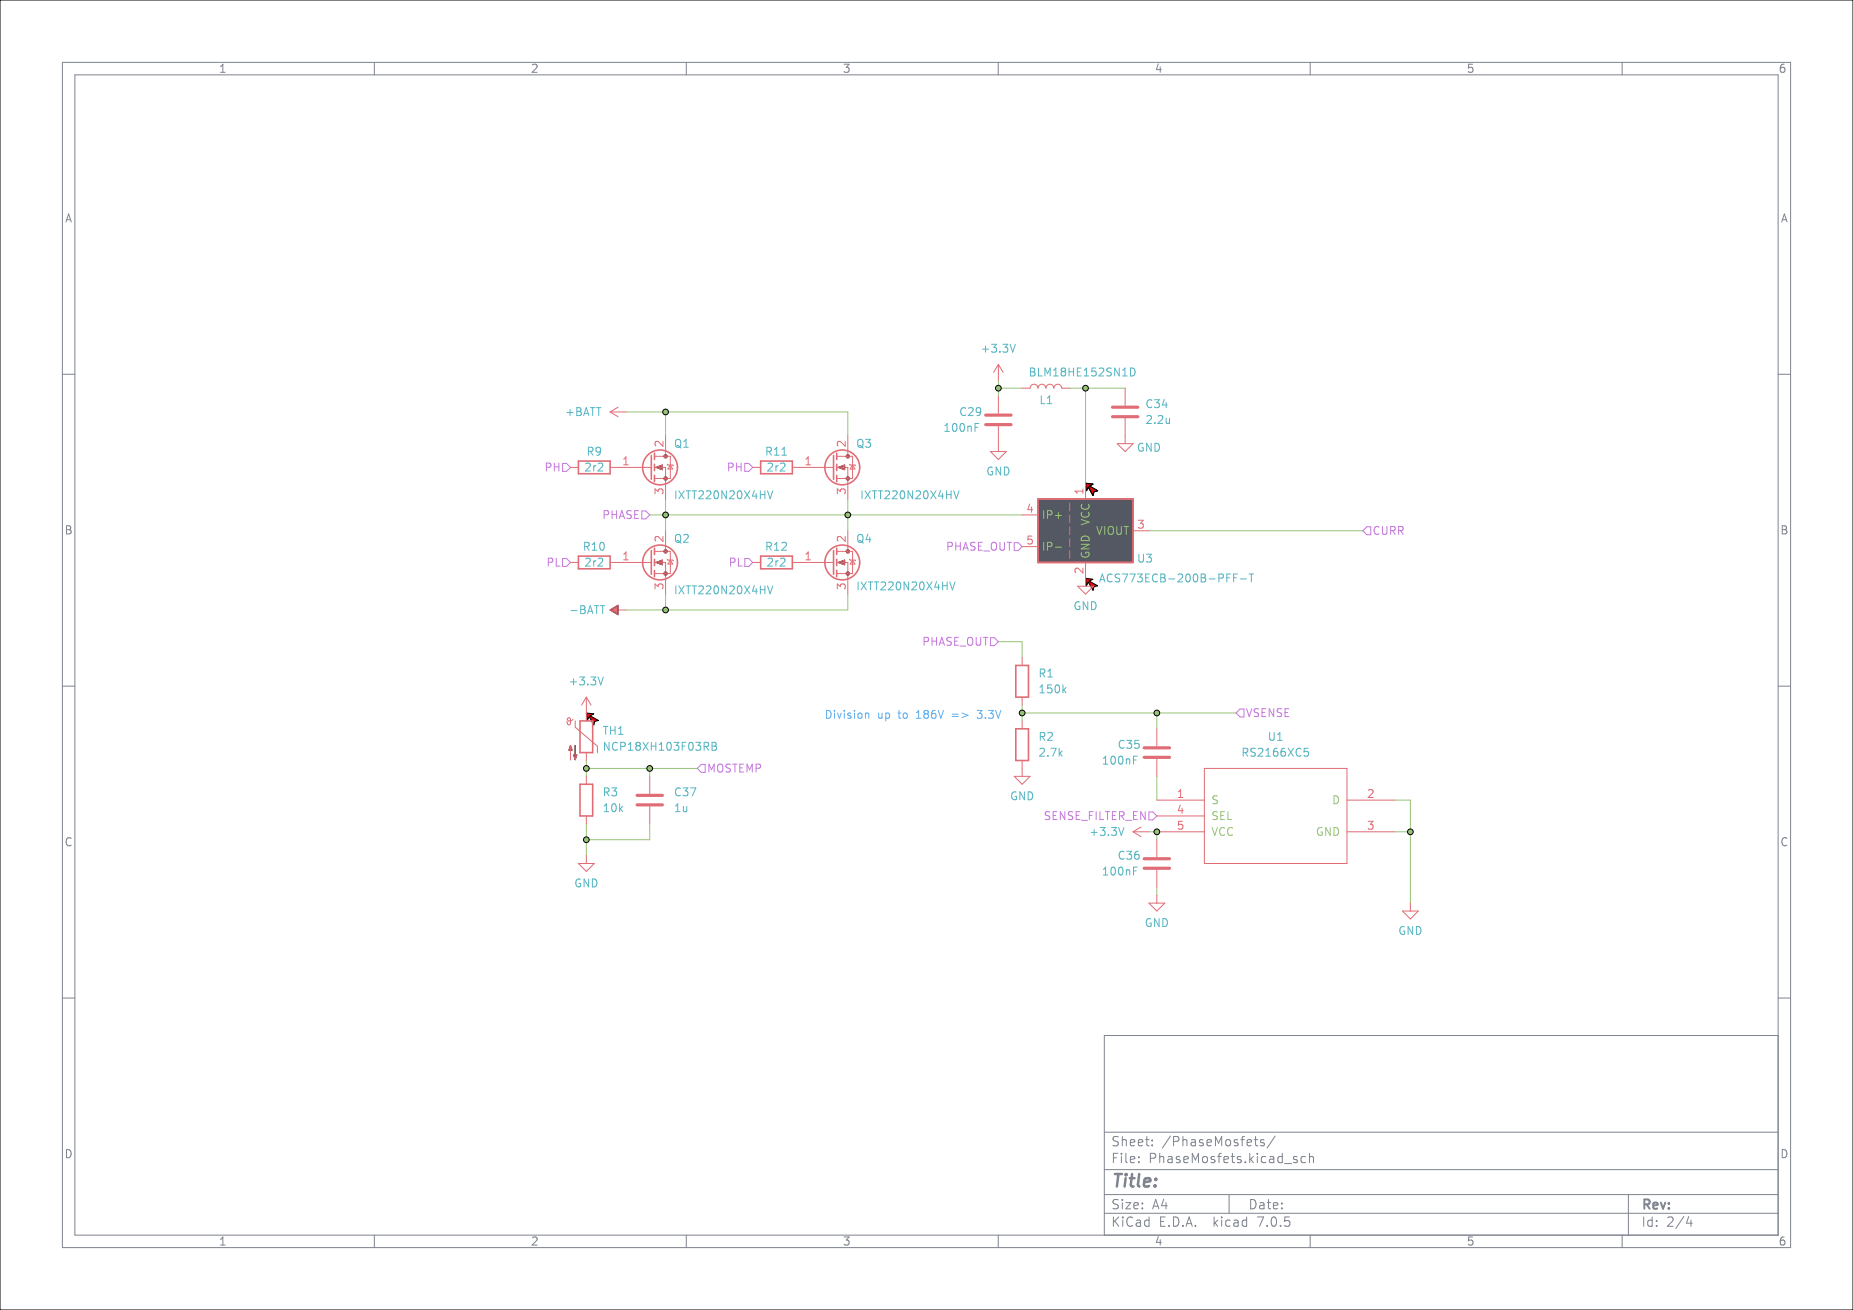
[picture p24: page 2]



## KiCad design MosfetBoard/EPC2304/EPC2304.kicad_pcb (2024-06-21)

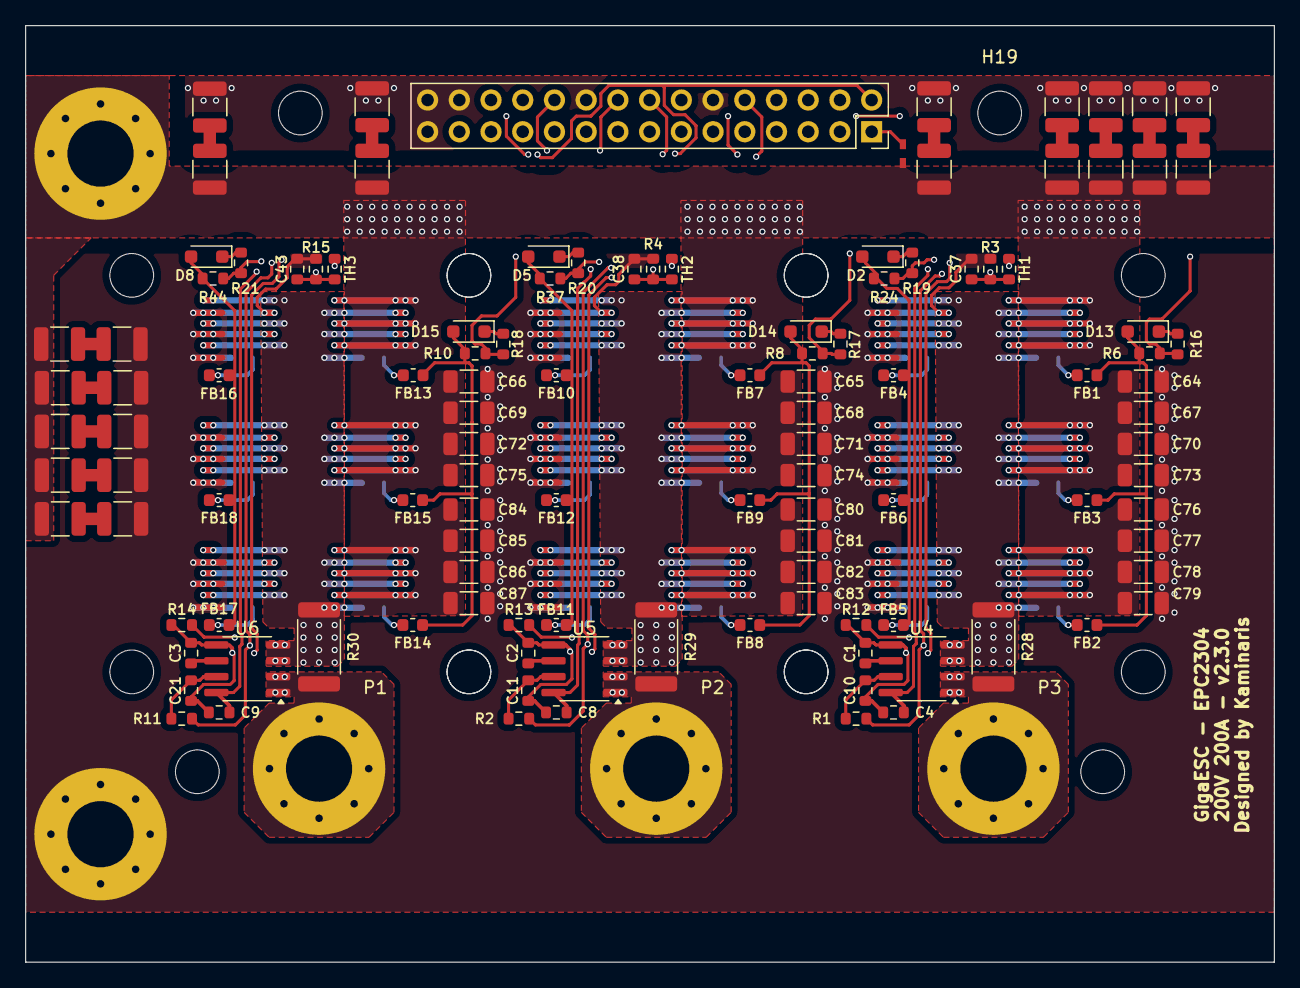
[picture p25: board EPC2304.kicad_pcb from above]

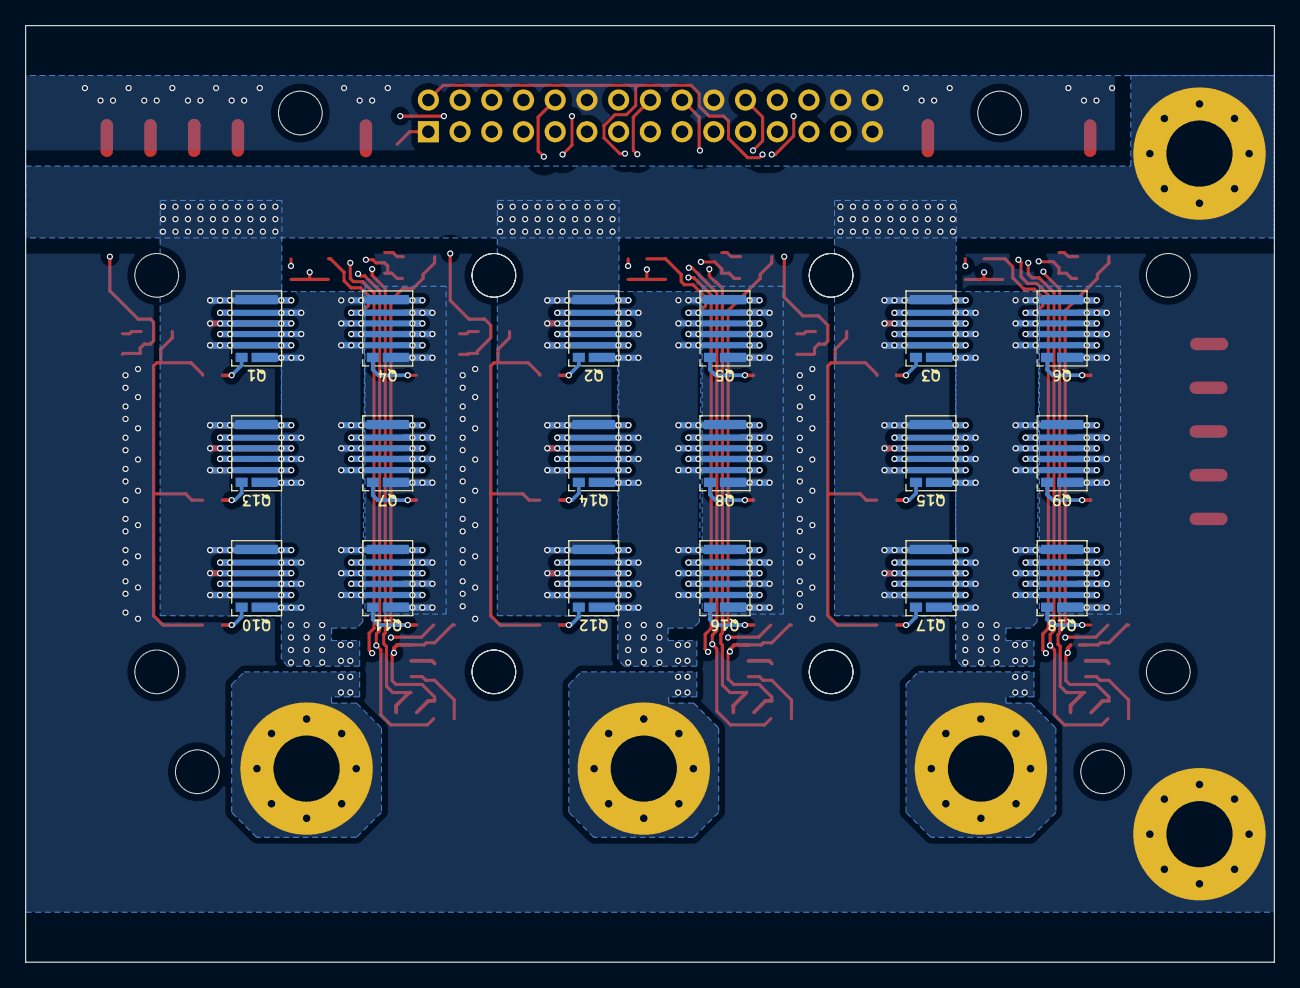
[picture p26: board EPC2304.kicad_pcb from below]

Board: 4 copper layers, 100.0 x 75.0 mm, 155 parts (18 on the bottom side), 74 nets.

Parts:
C1, C2, C3: 10n; C_0603_1608Metric_L
C4, C8, C9: 100n; C_0603_1608Metric_L
C10, C11, C21: 1n; C_0603_1608Metric_L
C37, C38, C43: 1u; C_0603_1608Metric_L
C64, C65, C66, C67, C68, C69, C70, C71, C72, C73, C74, C75, C76, C77, C78, C79, C80, C81, C82, C83, C84, C85, C86, C87: 200V 220n; C_1206_3216Metric
C88, C89, C90, C91, C92, C93, C94, C95, C96, C97, C98, C99, C100, C101, C102, C103, C104, C105, C106, C107, C108, C109, C110, C111: 10u 100V; C_1210_3225Metric
D2, D5, D8, D13, D14, D15: 1N5819WS; D_SOD-323_HandSoldering
FB1, FB2, FB3, FB4, FB5, FB6, FB7, FB8, FB9, FB10, FB11, FB12, FB13, FB14, FB15, FB16, FB17, FB18: BLM18AG331SN1D; L_0603_1608Metric
H1, H2, H3: PhaseConnector; MountingHole_5.3mm_M5_Pad_Via
H4, H6: MountingHole_Pad; MountingHole_5.3mm_M5_Pad_Via
H5, H7, H8, H9, H10, H11, H12, H13, H14, H15, H16, H17, H18, H19, H20, H21: MountingHole; CapHead_3.5mm
J2: LogicConnector; PinSocket_2x15_P2.54mm_Vertical
JP1: Jumper_2_Open; SolderJumper0.5mm_Open
Q1, Q2, Q3, Q4, Q5, Q6, Q7, Q8, Q9, Q10, Q11, Q12, Q13, Q14, Q15, Q16, Q17, Q18: EPC2304
R1, R2, R11: 4.7k; R_0603_1608Metric
R3, R4, R15: 10k; R_0603_1608Metric
R6, R8, R10, R24, R37, R44: 6.8; R_0603_1608Metric
R12, R13, R14: 9.1k; R_0603_1608Metric
R16, R17, R18, R19, R20, R21: 10; R_0603_1608Metric
R28, R29, R30: 0.3m; R_2512_6332Metric
TH1, TH2, TH3: NCP18XH103F03RB; R_0603_1608Metric
U4, U5, U6: MT9223CT-50BR5; SOIC-8_3.9x4.9mm_P1.27mm

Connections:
+BATT: C64.1, C65.1, C66.1, C67.1, C68.1, C69.1, C70.1, C71.1, C72.1, C73.1, C74.1, C75.1, C76.1, C77.1, C78.1, C79.1, C80.1, C81.1, C82.1, C83.1, C84.1, C85.1, C86.1, C87.1, C88.1, C90.1, C92.1, C94.1, C96.1, C98.1, C100.1, C102.1, C104.1, C106.1, C108.1, C110.1, H6.1, JP1.1 (A), Q1.3 (D), Q1.5 (D), Q1.7 (D), Q2.3 (D), Q2.5 (D), Q2.7 (D), Q3.3 (D), Q3.5 (D), Q3.7 (D), Q10.3 (D), Q10.5 (D), Q10.7 (D), Q12.3 (D), Q12.5 (D), Q12.7 (D), Q13.3 (D), Q13.5 (D), Q13.7 (D), Q14.3 (D), Q14.5 (D), Q14.7 (D), Q15.3 (D), Q15.5 (D), Q15.7 (D), Q17.3 (D), Q17.5 (D), Q17.7 (D)
-BATT: C37.2, C38.2, C43.2, C64.2, C65.2, C66.2, C67.2, C68.2, C69.2, C70.2, C71.2, C72.2, C73.2, C74.2, C75.2, C76.2, C77.2, C78.2, C79.2, C80.2, C81.2, C82.2, C83.2, C84.2, C85.2, C86.2, C87.2, C89.2, C91.2, C93.2, C95.2, C97.2, C99.2, C101.2, C103.2, C105.2, C107.2, C109.2, C111.2, H4.1, J2.12, J2.20, J2.28, J2.29, J2.30, Q4.2 (S), Q4.4 (S), Q4.6 (S), Q5.2 (S), Q5.4 (S), Q5.6 (S), Q6.2 (S), Q6.4 (S), Q6.6 (S), Q7.2 (S), Q7.4 (S), Q7.6 (S), Q8.2 (S), Q8.4 (S), Q8.6 (S), Q9.2 (S), Q9.4 (S), Q9.6 (S), Q11.2 (S), Q11.4 (S), Q11.6 (S), Q16.2 (S), Q16.4 (S), Q16.6 (S), Q18.2 (S), Q18.4 (S), Q18.6 (S), R3.2, R4.2, R15.2
/3.3V: J2.2, TH1.1, TH2.1, TH3.1
/5V: C4.2, C8.2, C9.2, J2.4, U4.8 (VCC), U5.8 (VCC), U6.8 (VCC)
/PH1: J2.6, R6.1, R16.1
/PH2: J2.14, R8.1, R17.1
/PH3: J2.22, R10.1, R18.1
/PHASE1: J2.8, Q1.2 (S), Q1.4 (S), Q1.6 (S), Q4.3 (D), Q4.5 (D), Q4.7 (D), Q7.3 (D), Q7.5 (D), Q7.7 (D), Q10.2 (S), Q10.4 (S), Q10.6 (S), Q11.3 (D), Q11.5 (D), Q11.7 (D), Q13.2 (S), Q13.4 (S), Q13.6 (S), R28.1, U4.3 (IP-), U4.4 (IP-)
/PHASE2: J2.16, Q2.2 (S), Q2.4 (S), Q2.6 (S), Q5.3 (D), Q5.5 (D), Q5.7 (D), Q8.3 (D), Q8.5 (D), Q8.7 (D), Q12.2 (S), Q12.4 (S), Q12.6 (S), Q14.2 (S), Q14.4 (S), Q14.6 (S), Q16.3 (D), Q16.5 (D), Q16.7 (D), R29.1, U5.3 (IP-), U5.4 (IP-)
/PHASE3: J2.24, Q3.2 (S), Q3.4 (S), Q3.6 (S), Q6.3 (D), Q6.5 (D), Q6.7 (D), Q9.3 (D), Q9.5 (D), Q9.7 (D), Q15.2 (S), Q15.4 (S), Q15.6 (S), Q17.2 (S), Q17.4 (S), Q17.6 (S), Q18.3 (D), Q18.5 (D), Q18.7 (D), R30.1, U6.3 (IP-), U6.4 (IP-)
/PL1: J2.10, R19.1, R24.1
/PL2: J2.18, R20.1, R37.1
/PL3: J2.26, R21.1, R44.1
/PhaseMosfets1/HIGH: D13.2 (A), FB1.1, FB2.1, FB3.1, R6.2
/PhaseMosfets1/LOW: D2.2 (A), FB4.1, FB5.1, FB6.1, R24.2
/PhaseMosfets1/MOS_TEMP: C37.1, J2.5, R3.1, TH1.2
/PhaseMosfets1/PHASE_OUT: H1.1, R28.2, U4.1 (IP+), U4.2 (IP+)
/PhaseMosfets1/SH+: J2.11, R1.1, R12.2
/PhaseMosfets1/SH-: C1.2, C4.1, C10.2, J2.9, R12.1, U4.5 (GND)
/PhaseMosfets2/HIGH: D14.2 (A), FB7.1, FB8.1, FB9.1, R8.2
/PhaseMosfets2/LOW: D5.2 (A), FB10.1, FB11.1, FB12.1, R37.2
/PhaseMosfets2/MOS_TEMP: C38.1, J2.13, R4.1, TH2.2
/PhaseMosfets2/PHASE_OUT: H2.1, R29.2, U5.1 (IP+), U5.2 (IP+)
/PhaseMosfets2/SH+: J2.19, R2.1, R13.2
/PhaseMosfets2/SH-: C2.2, C8.1, C11.2, J2.17, R13.1, U5.5 (GND)
/PhaseMosfets3/HIGH: D15.2 (A), FB13.1, FB14.1, FB15.1, R10.2
/PhaseMosfets3/LOW: D8.2 (A), FB16.1, FB17.1, FB18.1, R44.2
/PhaseMosfets3/MOS_TEMP: C43.1, J2.21, R15.1, TH3.2
/PhaseMosfets3/PHASE_OUT: H3.1, R30.2, U6.1 (IP+), U6.2 (IP+)
/PhaseMosfets3/SH+: J2.27, R11.1, R14.2
/PhaseMosfets3/SH-: C3.2, C9.1, C21.2, J2.25, R14.1, U6.5 (GND)
unnamed: C88.2, C89.1
unnamed: C90.2, C91.1
unnamed: C92.2, C93.1
unnamed: C94.2, C95.1
unnamed: C96.2, C97.1
unnamed: C98.2, C99.1
unnamed: C100.2, C101.1
unnamed: C102.2, C103.1
unnamed: C104.2, C105.1
unnamed: C106.2, C107.1
unnamed: C108.2, C109.1
unnamed: C110.2, C111.1
unnamed: D2.1 (K), R19.2
unnamed: D5.1 (K), R20.2
unnamed: D8.1 (K), R21.2
unnamed: D13.1 (K), R16.2
unnamed: D14.1 (K), R17.2
unnamed: D15.1 (K), R18.2
unnamed: J2.1, JP1.2 (B)
unnamed: FB1.2, Q1.1 (G)
unnamed: FB7.2, Q2.1 (G)
unnamed: FB13.2, Q3.1 (G)
unnamed: FB4.2, Q4.1 (G)
unnamed: FB10.2, Q5.1 (G)
unnamed: FB16.2, Q6.1 (G)
unnamed: FB6.2, Q7.1 (G)
unnamed: FB12.2, Q8.1 (G)
unnamed: FB18.2, Q9.1 (G)
unnamed: FB2.2, Q10.1 (G)
unnamed: FB5.2, Q11.1 (G)
unnamed: FB8.2, Q12.1 (G)
unnamed: FB3.2, Q13.1 (G)
unnamed: FB9.2, Q14.1 (G)
unnamed: FB15.2, Q15.1 (G)
unnamed: FB11.2, Q16.1 (G)
unnamed: FB14.2, Q17.1 (G)
unnamed: FB17.2, Q18.1 (G)
unnamed: C1.1, U4.6 (FILTER)
unnamed: C10.1, R1.2, U4.7 (VIOUT)
unnamed: C2.1, U5.6 (FILTER)
unnamed: C11.1, R2.2, U5.7 (VIOUT)
unnamed: C3.1, U6.6 (FILTER)
unnamed: C21.1, R11.2, U6.7 (VIOUT)

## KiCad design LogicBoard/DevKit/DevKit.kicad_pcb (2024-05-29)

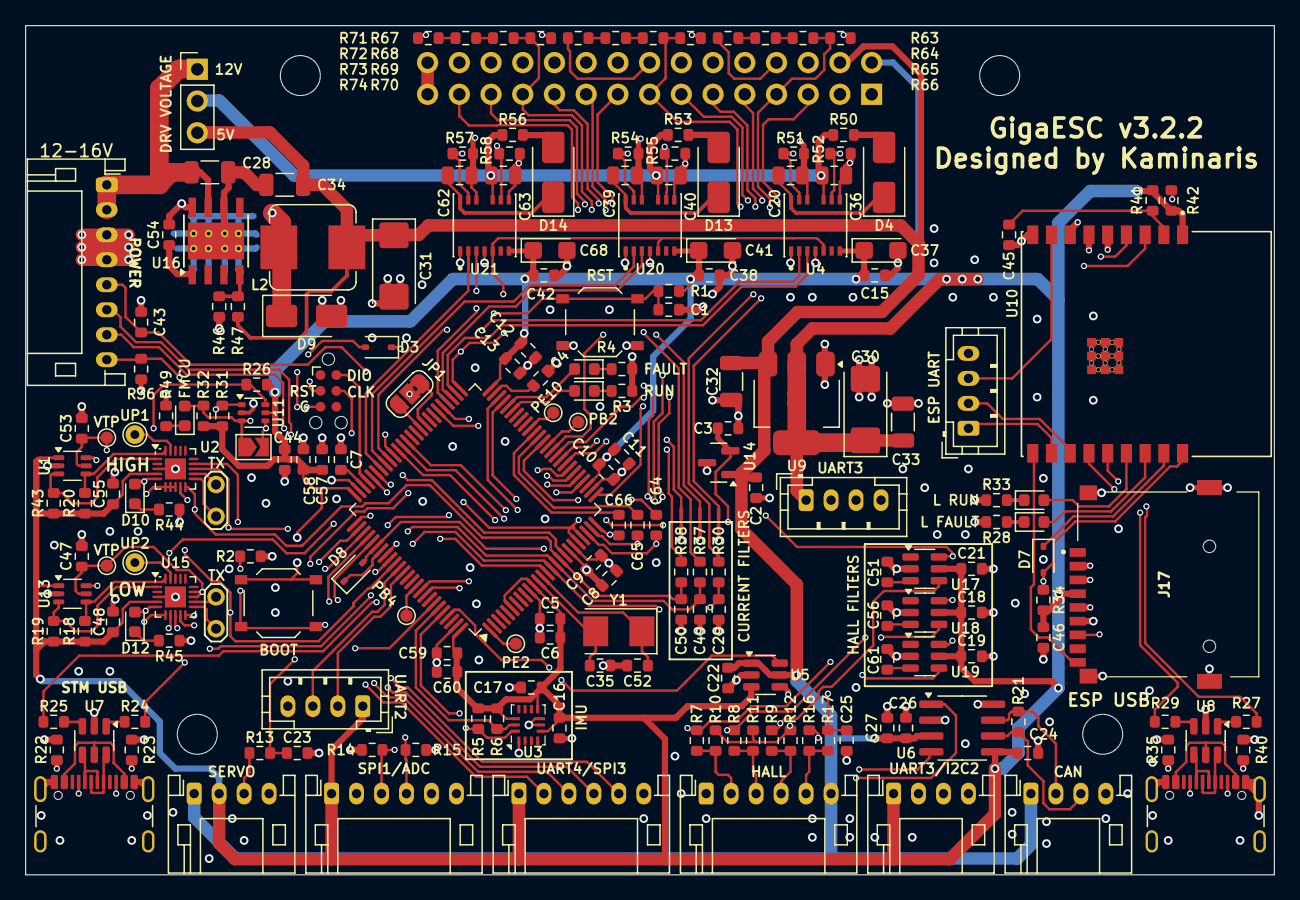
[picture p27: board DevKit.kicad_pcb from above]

Board: 4 copper layers, 100.0 x 68.0 mm, 208 parts (1 on the bottom side), 170 nets.

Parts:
C1, C6, C9, C11, C13, C15, C16, C17, C18, C19, C21, C22, C23, C24, C26, C38, C42, C44, C45, C46, C58, C60, C64, C65, C66: 100n; C_0603_1608Metric_L
C2, C3, C4, C7, C47, C48, C53, C55: 1u; C_0603_1608Metric_L
C5, C8, C10, C12, C54, C57, C59: 10n; C_0603_1608Metric_L
C20, C36, C39, C40, C62, C63: 4.7u 25v; C_0805_2012Metric
C25, C43, C51, C56, C61: 1n; C_0603_1608Metric_L
C27: 2.2u; C_0603_1608Metric_L
C28, C32, C33, C34: 22u 25V; C_1206_3216Metric
C29, C49, C50: 2.2n; C_0603_1608Metric_L
C30, C31: 100uF 10V Tant; CP_EIA-6032-28_Kemet-C
C35, C52: 20p; R_0603_1608Metric
C37, C41, C68: 47u 6.3v Tant; CP_EIA-3216-18_Kemet-A
D1, D5: L RUN; LED_0603_1608Metric
D2, D6, D10, D12: L FAULT; LED_0603_1608Metric
D3, D7, D8: 1N5819WS; D_SOD-323
D4, D13, D14: SS520F; D_SMA
D9: SS34; D_SMA
D11: DRV-FAULT; LED_0603_1608Metric
H1, H2, H3, H4: MountingHole; MountingHole_3.2mm_M3_ISO14580
J1: ServoConn; JST_PH_S4B-PH-K_1x04_P2.00mm_Horizontal
J2: AuxConn; JST_PH_S8B-PH-K_1x08_P2.00mm_Horizontal
J4, J21: UARTDBG; TestPoint_2Pads_Pitch2.54mm_Drill0.8mm
J5: HallConn; JST_PH_S6B-PH-K_1x06_P2.00mm_Horizontal
J6: UARTConn; JST_PH_S4B-PH-K_1x04_P2.00mm_Horizontal
J7: JTAG; Tag-Connect_TC2030-IDC-NL_2x03_P1.27mm_Vertical
J8: CANConn; JST_PH_S4B-PH-K_1x04_P2.00mm_Horizontal
J9, J13: USBC Socket; USB_C_Receptacle_GCT_USB4105-xx-A_16P_TopMnt_Horizontal
J10: LogicConnector; PinHeader_2x15_P2.54mm_Vertical
J11: SPI1Conn; JST_PH_S6B-PH-K_1x06_P2.00mm_Horizontal
J12: UART2Conn; JST_PH_B4B-PH-K_1x04_P2.00mm_Vertical
J15: ESPUartConn; JST_PH_B4B-PH-K_1x04_P2.00mm_Vertical
J17: MicroSD; TF01A
J20: SPI3Conn; JST_PH_S6B-PH-K_1x06_P2.00mm_Horizontal
J22: UART3Conn; JST_PH_B4B-PH-K_1x04_P2.00mm_Vertical
J23: DriverVoltageSelect; PinHeader_1x03_P2.54mm_Vertical
JP1: ServoSelector; SolderJumper-3_P1.3mm_Bridged2Bar12_RoundedPad1.0x1.5mm_Num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
JP2, JP3, JP4: GND Jumper; SolderJumper0.3mm
JP5: OV BYPASS; SolderJumper-2_P1.3mm_Open_TrianglePad1.0x1.5mm
L2: 15uH; L_Bourns_SRP7028A_7.3x6.6mm
R1, R3, R4, R7, R8, R9, R10, R11, R12, R14, R15, R16, R17, R26, R28, R31, R32, R33, R34, R36, R41, R42, R44, R45, R47, R49: 10k; R_0603_1608Metric
R2, R46: 3.3k; R_0603_1608Metric
R5, R6, R18, R19, R20, R43, R51, R52, R54, R55, R57, R58: 4.7k; R_0603_1608Metric
R13: 220; R_0603_1608Metric
R21: 120; R_0603_1608Metric
R22, R23, R35, R40: 5.1k; R_0603_1608Metric
R24, R25, R27, R29: 22; R_0603_1608Metric
R30, R37, R38: 150; R_0603_1608Metric
R50, R53, R56: 2.2; R_0603_1608Metric
R63, R64, R65, R67, R68, R69, R71, R72, R73: 348k; R_0603_1608Metric
R66, R70, R74: 18.7k; R_0603_1608Metric
SW1: BOOT; SW_Push_1P1T_XKB_TS-1187A
SW3: RST; SW_Push_1P1T_XKB_TS-1187A
TP2: TestPoint; TestPoint_Pad_D1.0mm
TP3, TP4: VTP; TestPoint_Pad_D1.0mm
TP5, TP6: UPDI; TestPoint_THTPad_D1.5mm_Drill0.7mm
TP7: PE2; TestPoint_Pad_D1.0mm
TP8: PB2; TestPoint_Pad_D1.0mm
TP9: PE10; TestPoint_Pad_D1.0mm
U1, U13: TPL0401B-10DCKR; Texas_R-PDSO-G6
U2, U15: ATTINY1616-MNR; VQFN-20-1EP_3x3mm_P0.4mm_EP1.7x1.7mm
U3: LSM6DS3TR-C; Bosch_LGA-14_3x2.5mm_P0.5mm
U4, U20, U21: 2EDF7275KXUMA1; IC_2EDF7275KXUMA2
U5, U17, U18, U19: RS2057XH; SOT-23-6
U6: TJA1050T/CM,118; SOIC-8_3.9x4.9mm_P1.27mm
U7, U8: USBLC6-2SC6; SOT-23-6
U9: AMS1117-3.3; SOT-223-3_TabPin2
U10: ESP32-C3-WROOM-02-N4; MODULE_ESP32-C3-WROOM-02-H4
U11: SN74LVC1G332DCKR; SOT-363_SC-70-6
U12: STM32F407VGT6; LQFP-100_14x14mm_P0.5mm
U14: REF3033AIDBZR; SOT-23
U16: TPS5430DDAR; TI_SO-PowerPAD-8_ThermalVias
Y1: X50328MSB2GI; Crystal_SMD_5032-2Pin_5.0x3.2mm

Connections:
+3.3REF: C3.1, U1.6 (H), U12.21 (VREF+), U12.22 (VDDA), U13.6 (H), U14.2 (Vout)
+3.3V: C5.1, C6.1, C8.1, C9.1, C10.1, C11.1, C12.1, C13.1, C15.2, C16.1, C17.1, C18.1, C19.1, C21.1, C24.1, C30.1, C33.1, C37.1, C38.2, C41.1, C42.2, C44.1, C46.1, C48.1, C55.1, C57.1, C58.1, C59.1, C60.1, C68.1, J1.2, J6.1, J10.2, J11.1, J12.1, J17.4 (VDD), J20.1, J22.1, R1.1, R5.1, R6.1, R16.2, R18.1, R19.1, R20.1, R26.1, R31.1, R32.1, R34.1, R41.2, R42.1, R43.1, SW1.1, U1.1 (VDD), U2.4 (VCC), U3.5 (VDDIO), U3.8 (VDD), U3.12 (CSB), U4.7 (VDDI), U5.3 (NC), U6.5 (VIO), U9.2 (VO), U10.1 (3V3), U11.5 (VCC), U12.6 (VBAT), U12.11 (VDD), U12.19 (VDD), U12.28 (VDD), U12.50 (VDD), U12.75 (VDD), U12.100 (VDD), U13.1 (VDD), U15.4 (VCC), U17.5 (V+), U18.5 (V+), U19.5 (V+), U20.7 (VDDI), U21.7 (VDDI)
+5V: C2.1, C22.1, C26.1, C27.1, C31.1, C32.1, C34.1, J1.1, J5.6, J8.1, J10.4, J23.3, L2.2, R47.2, U5.1 (NO), U5.5 (V+), U6.3 (VCC), U9.3 (VI), U14.1 (Vin)
+15V: C28.1, J2.1, J2.2, J23.1, U16.7 (VIN)
/CURR1-: J10.9, JP4.2 (B)
/CURR2-: J10.17, JP3.2 (B)
/CURR3-: J10.25, JP2.2 (B)
/DriverSocketPhase1/PH: J10.6, R51.2, U4.12 (OUTA)
/DriverSocketPhase1/PHASE: C20.2, J10.8, R51.1, R63.1, U4.11 (GNDA)
/DriverSocketPhase1/PHASE GROUND: C36.2, J10.12, R52.1, U4.8 (GNDB)
/DriverSocketPhase1/PL: J10.10, R52.2, U4.9 (OUTB)
/DriverSocketPhase2/PH: J10.14, R54.2, U20.12 (OUTA)
/DriverSocketPhase2/PHASE: C39.2, J10.16, R54.1, R67.1, U20.11 (GNDA)
/DriverSocketPhase2/PHASE GROUND: C40.2, J10.20, R55.1, U20.8 (GNDB)
/DriverSocketPhase2/PL: J10.18, R55.2, U20.9 (OUTB)
/DriverSocketPhase3/PH: J10.22, R57.2, U21.12 (OUTA)
/DriverSocketPhase3/PHASE: C62.2, J10.24, R57.1, R71.1, U21.11 (GNDA)
/DriverSocketPhase3/PHASE GROUND: C63.2, J10.28, R58.1, U21.8 (GNDB)
/DriverSocketPhase3/PL: J10.26, R58.2, U21.9 (OUTB)
/HardwareProtection/ComparatorHigh/AT RX: J21.2, U2.11 (PB3)
/HardwareProtection/ComparatorHigh/AT TX: J21.1, U2.12 (PB2)
/HardwareProtection/ComparatorHigh/ATTINY SCL: R43.2, U1.3 (SCL), U2.1 (PA2)
/HardwareProtection/ComparatorHigh/ATTINY SDA: R20.2, U1.4 (SDA), U2.20 (PA1)
/HardwareProtection/ComparatorHigh/CMP1-: C53.1, TP3.1, U1.5 (W), U2.6 (PA5), U2.7 (PA6), U2.8 (PA7)
/HardwareProtection/ComparatorHigh/LATCH OUT: D10.2 (A), R26.2, U2.5 (PA4), U11.6
/HardwareProtection/ComparatorLow/AT RX: J4.2, U15.11 (PB3)
/HardwareProtection/ComparatorLow/AT TX: J4.1, U15.12 (PB2)
/HardwareProtection/ComparatorLow/ATTINY SCL: R19.2, U13.3 (SCL), U15.1 (PA2)
/HardwareProtection/ComparatorLow/ATTINY SDA: R18.2, U13.4 (SDA), U15.20 (PA1)
/HardwareProtection/ComparatorLow/CMP1+: C47.1, TP4.1, U13.5 (W), U15.10 (PB4), U15.13 (PB1), U15.14 (PB0)
/HardwareProtection/ComparatorLow/LATCH OUT: D12.2 (A), R31.2, U11.1, U15.5 (PA4)
ADC EXT: J11.3, R14.2, U12.30 (PA5)
ADC EXT2: J11.4, R15.1, U12.31 (PA6)
AUX ENABLE: J2.6, U12.83 (PD2)
AUX FAULT: J2.7, U12.84 (PD3)
BOOT: R2.1, SW1.2, U12.94 (BOOT0)
CAN2 RX: D7.2 (A), D8.2 (A), R34.2, U10.18 (IO0), U12.81 (PD0)
CAN2 TX: D8.1 (K), U12.82 (PD1)
CAN RX: U6.4 (RXD), U12.91 (PB5)
CAN TX: U6.1 (TXD), U12.92 (PB6)
CLEAR HW FAULT: J2.8, R36.1, U2.9 (PB5), U12.85 (PD4), U15.9 (PB5)
CURR1: J10.11, R30.2
CURR1 FILTERED: C29.1, R30.1, U2.13 (PB1), U12.15 (PC0), U15.7 (PA6)
CURR2: J10.19, R37.2
CURR2 FILTERED: C49.1, R37.1, U2.14 (PB0), U12.16 (PC1), U15.8 (PA7)
CURR3: J10.27, R38.2
CURR3 FILTERED: C50.2, R38.1, U2.10 (PB4), U12.17 (PC2), U15.6 (PA5)
DRIVER POWER: C36.1, C40.1, C63.1, J23.2, R50.1, R53.1, R56.1, U4.10 (VDDB), U20.10 (VDDB), U21.10 (VDDB)
ESP FAULT LED: D6.2 (A), U10.16 (IO2)
ESP IO9: J15.3, U10.8 (IO9)
ESP MISO: J17.7 (DAT0), U10.5 (IO6)
ESP MOSI: J17.3 (CMD), U10.3 (IO4)
ESP RUN LED: D5.2 (A), U10.15 (IO3)
ESP RX: J15.1, U10.11 (RXD)
ESP SCK: J17.5 (CLK), U10.4 (IO5)
ESP SD CS: J17.2 (DAT3/CD), U10.6 (IO7)
ESP SD DETECT: J17.9 (DET), U10.10 (IO10)
ESP TX: J15.2, U10.12 (TXD)
ESP USB D+: R27.2, U10.14 (IO19)
ESP USB D-: R29.2, U10.13 (IO18)
GND: C1.2, C2.2, C3.2, C4.2, C5.2, C6.2, C7.2, C8.2, C9.2, C10.2, C11.2, C12.2, C13.2, C15.1, C16.2, C17.2, C18.2, C19.2, C21.2, C22.2, C23.2, C24.2, C25.2, C26.2, C27.2, C28.2, C29.2, C30.2, C31.2, C32.2, C33.2, C34.2, C35.1, C37.2, C38.1, C41.2, C42.1, C43.2, C44.2, C45.2, C46.2, C47.2, C48.2, C49.2, C50.1, C51.1, C52.2, C53.2, C55.2, C56.1, C57.2, C58.2, C59.2, C60.2, C61.1, C68.2, D9.2 (A), J1.4, J2.3, J2.4, J5.1, J6.4, J7.5 (GND), J8.4, J9.A1 (GND), J9.A12 (GND), J9.B1 (GND), J9.B12 (GND), J9.S1 (SHIELD), J10.29, J10.30, J11.6, J12.4, J13.A1 (GND), J13.A12 (GND), J13.B1 (GND), J13.B12 (GND), J13.S1 (SHIELD), J15.4, J17.6 (VSS), J17.10 (SHIELD), J20.6, J22.4, JP2.1 (A), JP3.1 (A), JP4.1 (A), R2.2, R3.2, R4.2, R14.1, R15.2, R22.1, R23.1, R28.2, R33.2, R35.1, R36.2, R40.1, R44.2, R45.2, R46.2, R49.2, R66.2, R70.2, R74.2, SW3.2, U1.2 (GND), U2.3 (GND), U2.21 (GND), U3.1 (SDO), U3.6 (GNDIO), U3.7 (GND), U4.1 (GNDI), U4.4 (SLDON), U5.2 (GND), U6.2 (GND), U6.8 (S), U7.2 (GND), U8.2 (GND), U9.1 (GND), U10.9 (GND), U10.19 (GND), U10.20 (GND), U10.21 (GND), U10.22 (GND), U10.23 (GND), U10.24 (GND), U10.25 (GND), U10.26 (GND), U10.27 (GND), U10.28 (GND), U10.29 (GND), U10.30 (GND), U10.31 (GND), U10.32 (GND), U10.33 (GND), U10.34 (GND), U10.35 (GND), U10.36 (GND), U10.37 (GND), U10.38 (GND), U10.39 (GND), U11.2 (GND), U12.10 (VSS), U12.20 (VSSA), U12.27 (VSS), U12.74 (VSS), U12.99 (VSS), U13.2 (GND), U14.3 (GND), U15.3 (GND), U15.21 (GND), U16.6 (GND), U16.9 (GNDPAD), U17.2 (GND), U18.2 (GND), U19.2 (GND), U20.1 (GNDI), U20.4 (SLDON), U21.1 (GNDI), U21.4 (SLDON)
H1: U4.2 (INA), U12.67 (PA8)
H2: U12.68 (PA9), U20.2 (INA)
H3: U12.69 (PA10), U21.2 (INA)
HALL1: R9.1, U12.63 (PC6), U17.4 (COM)
HALL1 IN: J5.4, R9.2, R12.1
HALL2: R8.1, U12.64 (PC7), U18.4 (COM)
HALL2 IN: J5.3, R8.2, R11.1
HALL3: R7.1, U12.65 (PC8), U19.4 (COM)
HALL3 IN: J5.2, R7.2, R10.1
HALL FILTER ENABLE: U12.34 (PC5), U17.6 (IN), U18.6 (IN), U19.6 (IN)
I2C2 SCL/USART3 TX: J6.3, U12.47 (PB10)
I2C2 SDA/USART3 RX: J6.2, U12.48 (PB11)
IMU SCL: R6.2, U3.13 (SCx), U12.95 (PB8)
IMU SDA: R5.2, U3.14 (SDx), U12.96 (PB9)
IN V: C43.1, J2.5, U12.18 (PC3)
L1: U4.3 (INB), U12.52 (PB13)
L2: U12.53 (PB14), U20.3 (INB)
L3: U12.54 (PB15), U21.3 (INB)
LED FAULT: D2.2 (A), U12.46 (PE15)
LED RUN: D1.2 (A), U12.45 (PE14)
MOSTEMP1: J10.5, U12.26 (PA3)
MOSTEMP2: J10.13, U12.35 (PB0)
MOSTEMP3: J10.21, U12.36 (PB1)
NRST: C1.1, J7.3 (~RESET), R1.2, SW3.1, U12.14 (NRST)
unnamed: D1.1 (K), R3.1
unnamed: D2.1 (K), R4.1
unnamed: D3.2 (A), JP5.2 (B), U11.4
unnamed: D4.2 (A), R50.2
unnamed: C20.1, D4.1 (K), U4.13 (VDDA)
unnamed: D5.1 (K), R33.1
unnamed: D6.1 (K), R28.1
unnamed: D7.1 (K), U10.17 (IO1)
unnamed: C54.1, D9.1 (K), L2.1, U16.8 (PH)
unnamed: D10.1 (K), R44.1
unnamed: D11.1 (K), R49.1
unnamed: D12.1 (K), R45.1
unnamed: D13.2 (A), R53.2
unnamed: C39.1, D13.1 (K), U20.13 (VDDA)
unnamed: D14.2 (A), R56.2
unnamed: C62.1, D14.1 (K), U21.13 (VDDA)
unnamed: J1.3, R13.1
unnamed: J8.2, R21.2, U6.7 (CANH)
unnamed: J8.3, R21.1, U6.6 (CANL)
unnamed: J9.A5 (CC1), R22.2
unnamed: J9.B5 (CC2), R23.2
unnamed: J9.A6 (D+), J9.B6 (D+), U7.6 (I/O1)
unnamed: J9.A7 (D-), J9.B7 (D-), U7.4 (I/O2)
unnamed: J13.A5 (CC1), R35.2
unnamed: J13.B5 (CC2), R40.2
unnamed: J13.A6 (D+), J13.B6 (D+), U8.6 (I/O1)
unnamed: J13.A7 (D-), J13.B7 (D-), U8.4 (I/O2)
unnamed: JP1.1 (A), U12.59 (PD12)
unnamed: JP1.3 (B), U12.60 (PD13)
unnamed: R24.1, U7.1 (I/O1)
unnamed: R25.1, U7.3 (I/O2)
unnamed: R27.1, U8.1 (I/O1)
unnamed: R29.1, U8.3 (I/O2)
unnamed: R63.2, R64.1
unnamed: R64.2, R65.1
unnamed: R67.2, R68.1
unnamed: R68.2, R69.1
unnamed: R71.2, R72.1
unnamed: R72.2, R73.1
unnamed: TP5.1, U2.19 (~RESET/PA0)
unnamed: R10.2, R11.2, R12.2, U5.4 (COM)
unnamed: J9.A4 (VBUS), J9.A9 (VBUS), J9.B4 (VBUS), J9.B9 (VBUS), U7.5 (VBUS)
unnamed: J13.A4 (VBUS), J13.A9 (VBUS), J13.B4 (VBUS), J13.B9 (VBUS), U8.5 (VBUS)
unnamed: C45.1, R41.1, U10.2 (EN)
unnamed: R42.2, U10.7 (IO8)
unnamed: TP8.1, U12.37 (PB2)
unnamed: TP2.1, U12.90 (PB4)
unnamed: TP7.1, U12.1 (PE2)
unnamed: TP9.1, U12.41 (PE10)
unnamed: C35.2, U12.12 (PH0), Y1.2
unnamed: C52.1, U12.13 (PH1), Y1.1
unnamed: C4.1, U12.49 (VCAP_1)
unnamed: C7.1, U12.73 (VCAP_2)
unnamed: TP6.1, U15.19 (~RESET/PA0)
unnamed: C54.2, U16.1 (BOOT)
unnamed: R46.1, R47.1, U16.4 (VSENSE)
unnamed: C51.2, U17.3 (NC)
unnamed: C56.2, U18.3 (NC)
unnamed: C61.2, U19.3 (NC)
PHASE FILTER ENABLE1: C64.2, U12.38 (PE7)
PHASE FILTER ENABLE2: C65.2, U12.39 (PE8)
PHASE FILTER ENABLE3: C66.2, U12.40 (PE9)
POWER STAGE DISABLE: D11.2 (A), JP5.1 (A), R32.2, U11.3, U12.66 (PC9)
POWER STAGE LOCKOUT: D3.1 (K), U4.5 (DISABLE), U12.51 (PB12), U20.5 (DISABLE), U21.5 (DISABLE)
SENSOR VOLTAGE SELECT: U5.6 (IN), U12.97 (PE0)
SERVO: C23.1, JP1.2 (C), R13.2
SPI1 MOSI: J11.5, U12.32 (PA7)
SPI1 NSS: J11.2, U12.29 (PA4)
SPI3 MISO: J20.4, U12.79 (PC11)
SPI3 MOSI: J20.5, U12.80 (PC12)
SPI3 NSS: J20.2, U12.77 (PA15)
SPI3 SCK: J20.3, U12.78 (PC10)
SWCLK: J7.4 (SWCLK), U12.76 (PA14)
SWDIO: J7.2 (SWDIO), U12.72 (PA13)
TEMPMOTOR: C25.1, R17.2, U12.33 (PC4)
TEMPMOTOR IN: J5.5, R16.1, R17.1
UART3 RX: J22.2, U12.56 (PD9)
UART3 TX: J22.3, U12.55 (PD8)
USART2 RX: J12.2, U12.87 (PD6)
USART2 TX: J12.3, U12.86 (PD5)
USBD+: R24.2, U12.71 (PA12)
USBD-: R25.2, U12.70 (PA11)
VSENSE1: C64.1, J10.7, R65.2, R66.1, U12.23 (PA0)
VSENSE2: C65.1, J10.15, R69.2, R70.1, U12.24 (PA1)
VSENSE3: C66.1, J10.23, R73.2, R74.1, U12.25 (PA2)

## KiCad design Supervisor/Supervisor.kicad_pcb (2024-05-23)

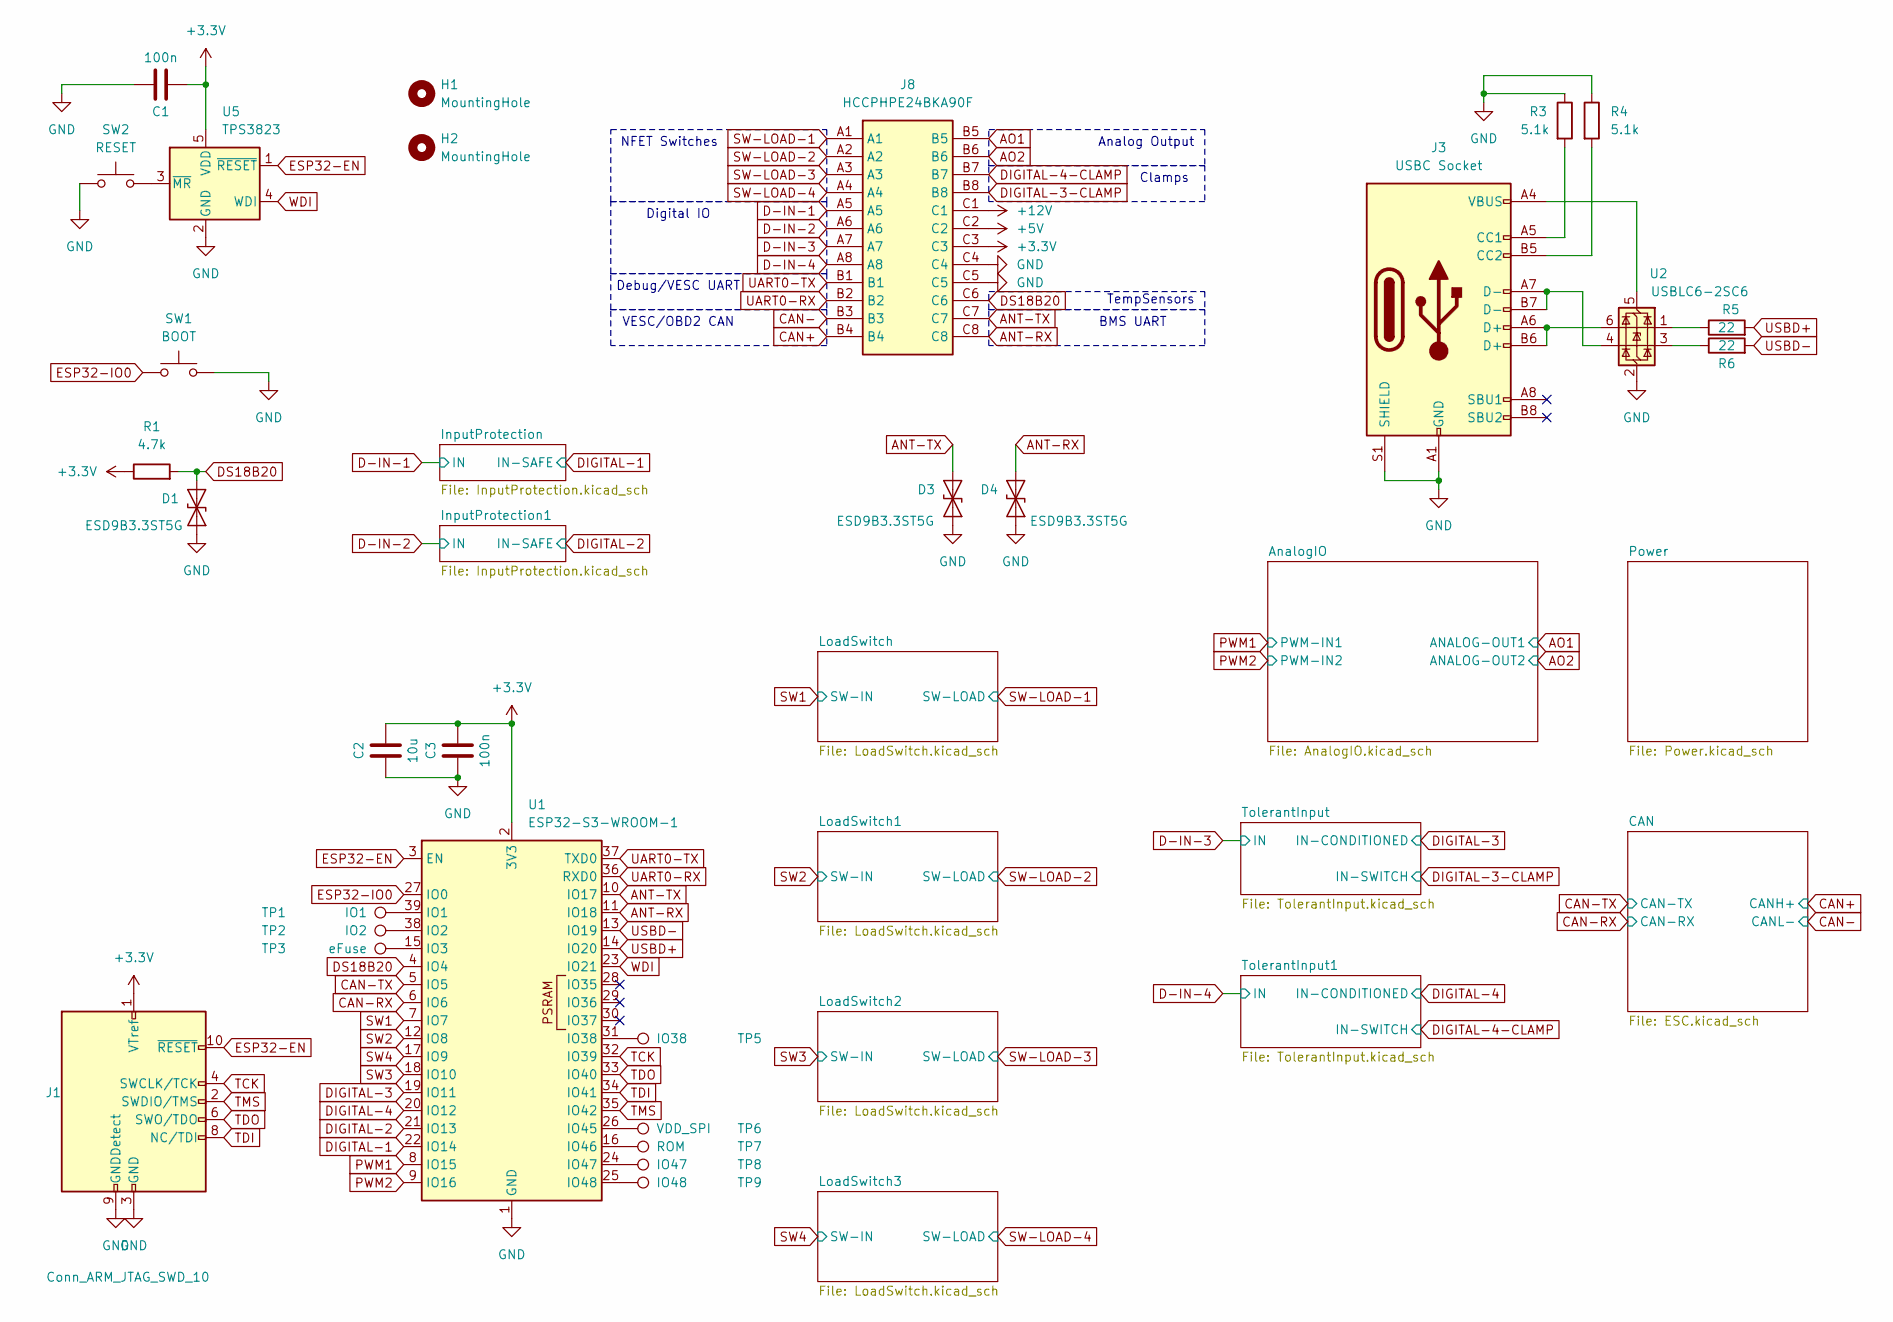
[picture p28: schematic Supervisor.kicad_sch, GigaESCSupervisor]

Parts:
C1, C3: 100n; C_0603_1608Metric; MPN C14663
C2: 10u; C_0603_1608Metric; MPN C19702
D1, D3, D4: ESD9B3.3ST5G; D_SOD-923; MPN C96512
H1, H2: MountingHole; MountingHole_3.2mm_M3
J1: Conn_ARM_JTAG_SWD_10; IDC-Header_2x05_P2.54mm_Vertical; MPN C429962
J3: USBC Socket; USB_C_Receptacle_GCT_USB4105-xx-A_16P_TopMnt_Horizontal; MPN C2765186; JLCPosOffset 0,1.27
J8: HCCPHPE24BKA90F; Manufacturer_Part_Number HCCPHPE24BKA90F; Mouser Part Number 649-HCCPHPE24BKA90F
R1: 4.7k; R_0603_1608Metric; MPN C23162
R3, R4: 5.1k; R_0603_1608Metric; MPN C23186
R5, R6: 22; R_0603_1608Metric; MPN C23345
SW1: BOOT; SW_Push_1P1T_XKB_TS-1187A; MPN C318884
SW2: RESET; SW_Push_1P1T_XKB_TS-1187A; MPN C318884
TP1: IO1; TestPoint_Pad_2.0x2.0mm
TP2: IO2; TestPoint_Pad_2.0x2.0mm
TP3: eFuse; TestPoint_Pad_2.0x2.0mm
TP5: IO38; TestPoint_Pad_2.0x2.0mm
TP6: VDD_SPI; TestPoint_Pad_2.0x2.0mm
TP7: ROM; TestPoint_Pad_2.0x2.0mm
TP8: IO47; TestPoint_Pad_2.0x2.0mm
TP9: IO48; TestPoint_Pad_2.0x2.0mm
U1: ESP32-S3-WROOM-1; MPN C2913202
U2: USBLC6-2SC6; SOT-23-6; MPN C2827654; JLCRotOffset -90
U5: TPS3823; SOT-23-5; MPN C7719

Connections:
+3.3V: C1.2, C2.1, C3.1, J1.1 (VTref), J8.C3, R1.1, U1.2 (3V3), U5.5 (VDD); also elsewhere on the board
+5V: J8.C2; also elsewhere on the board
+12V: J8.C1; also elsewhere on the board
ANT-RX: D4.1 (A1), J8.C8, U1.11 (IO18)
ANT-TX: D3.1 (A1), J8.C7, U1.10 (IO17)
AO1: J8.B5; also elsewhere on the board
AO2: J8.B6; also elsewhere on the board
CAN+: J8.B4; also elsewhere on the board
CAN-: J8.B3; also elsewhere on the board
CAN-RX: U1.6 (IO6); also elsewhere on the board
CAN-TX: U1.5 (IO5); also elsewhere on the board
D-IN-3: J8.A7; also elsewhere on the board
D-IN-4: J8.A8; also elsewhere on the board
DIGITAL-1: U1.22 (IO14); also elsewhere on the board
DIGITAL-2: U1.21 (IO13); also elsewhere on the board
DIGITAL-3-CLAMP: J8.B8; also elsewhere on the board
DIGITAL-4-CLAMP: J8.B7; also elsewhere on the board
DS18B20: D1.1 (A1), J8.C6, R1.2, U1.4 (IO4)
ESP32-EN: J1.10 (~RESET), U1.3 (EN), U5.1 (~RESET)
ESP32-IO0: SW1.1, U1.27 (IO0)
GND: C1.1, C2.2, C3.2, D1.2 (A2), D3.2 (A2), D4.2 (A2), J1.3 (GND), J1.5 (GND), J1.9 (GNDDetect), J3.A1 (GND), J3.A12 (GND), J3.B1 (GND), J3.B12 (GND), J3.S1 (SHIELD), J8.C4, J8.C5, R3.1, R4.1, SW1.2, SW2.1, U1.1 (GND), U1.40 (GND), U1.41 (GND), U2.2 (GND), U5.2 (GND); also elsewhere on the board
unnamed: J3.A5 (CC1), R3.2
unnamed: J3.B5 (CC2), R4.2
unnamed: J3.A6 (D+), J3.B6 (D+), U2.6 (I/O1)
unnamed: J3.A7 (D-), J3.B7 (D-), U2.4 (I/O2)
unnamed: R5.1, U2.1 (I/O1)
unnamed: R6.1, U2.3 (I/O2)
unnamed: TP1.1, U1.39 (IO1)
unnamed: TP2.1, U1.38 (IO2)
unnamed: TP3.1, U1.15 (IO3)
unnamed: TP5.1, U1.31 (IO38)
unnamed: TP6.1, U1.26 (IO45)
unnamed: TP7.1, U1.16 (IO46)
unnamed: TP8.1, U1.24 (IO47)
unnamed: TP9.1, U1.25 (IO48)
unnamed: J3.A4 (VBUS), J3.A9 (VBUS), J3.B4 (VBUS), J3.B9 (VBUS), U2.5 (VBUS)
unnamed: SW2.2, U5.3 (~MR)
PWM1: U1.8 (IO15); also elsewhere on the board
PWM2: U1.9 (IO16); also elsewhere on the board
SW1: U1.7 (IO7); also elsewhere on the board
SW2: U1.12 (IO8); also elsewhere on the board
SW3: U1.18 (IO10); also elsewhere on the board
SW4: U1.17 (IO9); also elsewhere on the board
SW-LOAD-1: J8.A1; also elsewhere on the board
SW-LOAD-2: J8.A2; also elsewhere on the board
SW-LOAD-3: J8.A3; also elsewhere on the board
SW-LOAD-4: J8.A4; also elsewhere on the board
TCK: J1.4 (SWCLK/TCK), U1.32 (IO39)
TDI: J1.8 (NC/TDI), U1.34 (IO41)
TDO: J1.6 (SWO/TDO), U1.33 (IO40)
TMS: J1.2 (SWDIO/TMS), U1.35 (IO42)
UART0-RX: J8.B2, U1.36 (RXD0)
UART0-TX: J8.B1, U1.37 (TXD0)
USBD+: R5.2, U1.14 (IO20)
USBD-: R6.2, U1.13 (IO19)
WDI: U1.23 (IO21), U5.4 (WDI)

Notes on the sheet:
TempSensors
Clamps
Digital IO
Analog Output
VESC/OBD2 CAN
NFET Switches
Debug/VESC UART
BMS UART

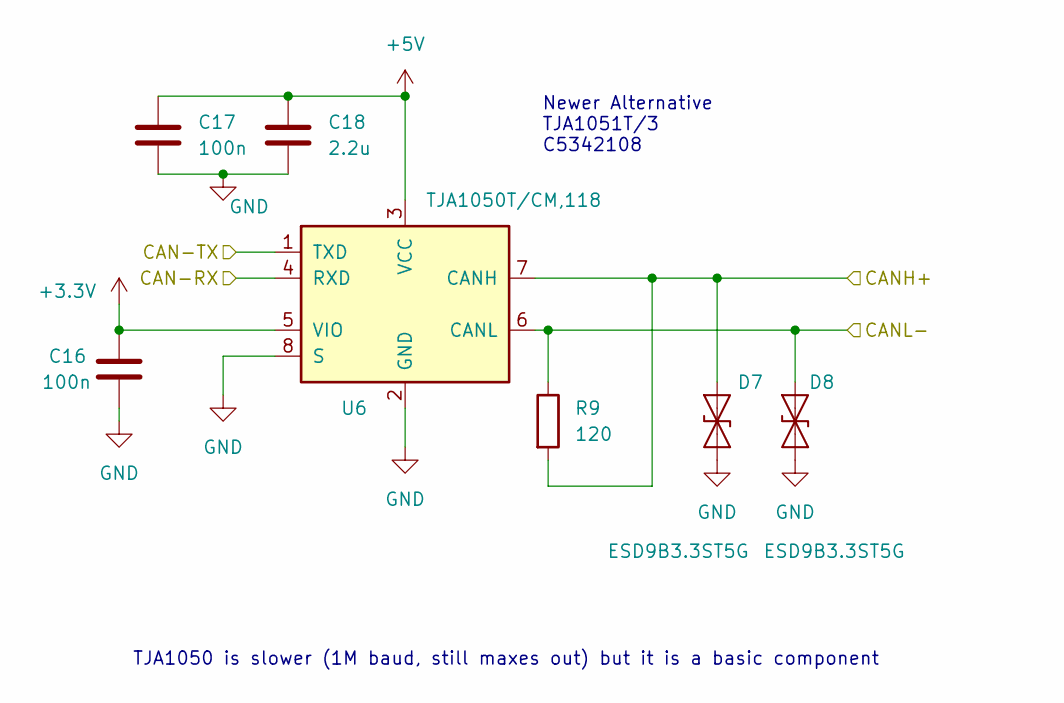
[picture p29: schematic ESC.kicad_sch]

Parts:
C16, C17: 100n; C_0603_1608Metric; MPN C14663
C18: 2.2u; C_0603_1608Metric; MPN C23630
D7, D8: ESD9B3.3ST5G; D_SOD-923; MPN C96512
R9: 120; R_0603_1608Metric; MPN C22787
U6: TJA1050T/CM,118; SOIC-8_3.9x4.9mm_P1.27mm; MPN C6952; JLCRotOffset -90

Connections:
+3.3V: C16.1, U6.5 (VIO); also elsewhere on the board
+5V: C17.1, C18.1, U6.3 (VCC); also elsewhere on the board
CAN+: D7.1 (A1), R9.2, U6.7 (CANH); also elsewhere on the board
CAN-: D8.1 (A1), R9.1, U6.6 (CANL); also elsewhere on the board
CAN-RX: U6.4 (RXD); also elsewhere on the board
CAN-TX: U6.1 (TXD); also elsewhere on the board
GND: C16.2, C17.2, C18.2, D7.2 (A2), D8.2 (A2), U6.2 (GND), U6.8 (S); also elsewhere on the board

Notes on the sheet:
TJA1050 is slower (1M baud, still maxes out) but it is a basic component
Newer Alternative TJA1051T/3 C5342108

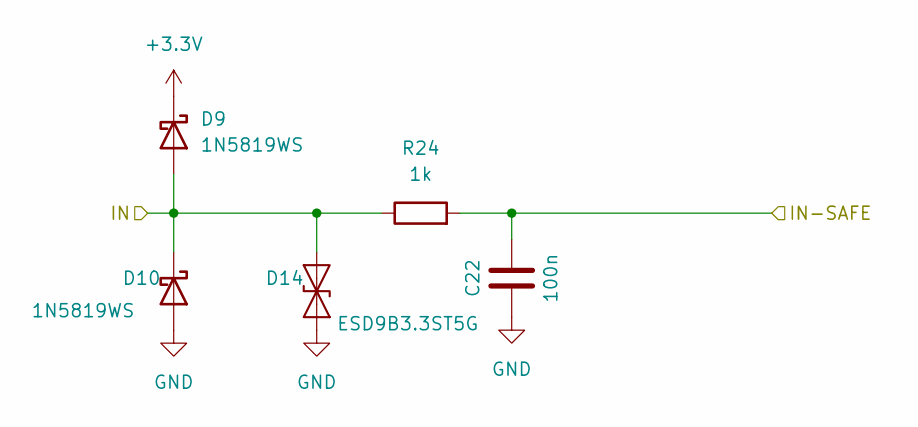
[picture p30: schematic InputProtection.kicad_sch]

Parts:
C22: 100n; C_0603_1608Metric; MPN C14663
D9, D10: 1N5819WS; D_SOD-323; MPN C191023
D14: ESD9B3.3ST5G; D_SOD-923; MPN C96512
R24: 1k; R_0603_1608Metric; MPN C21190

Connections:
+3.3V: D9.1 (K); also elsewhere on the board
DIGITAL-1: C22.1, R24.2; also elsewhere on the board
GND: C22.2, D10.2 (A), D14.2 (A2); also elsewhere on the board

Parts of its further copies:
C23: 100n; C_0603_1608Metric; MPN C14663
D11: ESD9B3.3ST5G; D_SOD-923; MPN C96512
D12, D13: 1N5819WS; D_SOD-323; MPN C191023
R25: 1k; R_0603_1608Metric; MPN C21190

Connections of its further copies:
+3.3V: D12.1 (K); also elsewhere on the board
DIGITAL-2: C23.1, R25.2; also elsewhere on the board
GND: C23.2, D11.2 (A2), D13.2 (A); also elsewhere on the board

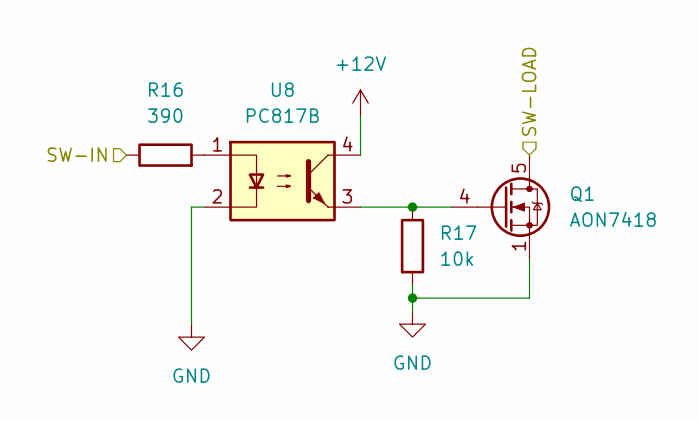
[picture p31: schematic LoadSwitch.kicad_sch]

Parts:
Q1: AON7418; VSON-8_3.3x3.3mm_P0.65mm_NexFET; MPN C74384
R16: 390; R_0603_1608Metric; MPN C23151
R17: 10k; R_0603_1608Metric; MPN C25804
U8: PC817B; SMDIP-4_W7.62mm; MPN C3025163

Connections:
+12V: U8.4; also elsewhere on the board
GND: Q1.1 (S), Q1.2 (S), Q1.3 (S), R17.2, U8.2; also elsewhere on the board
unnamed: Q1.4 (G), R17.1, U8.3
unnamed: R16.2, U8.1
SW1: R16.1; also elsewhere on the board
SW-LOAD-1: Q1.5 (D); also elsewhere on the board

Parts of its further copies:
Q2, Q3, Q4: AON7418; VSON-8_3.3x3.3mm_P0.65mm_NexFET; MPN C74384
R18, R20, R22: 390; R_0603_1608Metric; MPN C23151
R19, R21, R23: 10k; R_0603_1608Metric; MPN C25804
U9, U10, U11: PC817B; SMDIP-4_W7.62mm; MPN C3025163

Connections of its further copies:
+12V: U9.4, U10.4, U11.4; also elsewhere on the board
GND: Q2.1 (S), Q2.2 (S), Q2.3 (S), Q3.1 (S), Q3.2 (S), Q3.3 (S), Q4.1 (S), Q4.2 (S), Q4.3 (S), R19.2, R21.2, R23.2, U9.2, U10.2, U11.2; also elsewhere on the board
unnamed: Q2.4 (G), R19.1, U9.3
unnamed: Q3.4 (G), R21.1, U10.3
unnamed: Q4.4 (G), R23.1, U11.3
unnamed: R18.2, U9.1
unnamed: R20.2, U10.1
unnamed: R22.2, U11.1
SW2: R18.1; also elsewhere on the board
SW3: R20.1; also elsewhere on the board
SW4: R22.1; also elsewhere on the board
SW-LOAD-2: Q2.5 (D); also elsewhere on the board
SW-LOAD-3: Q3.5 (D); also elsewhere on the board
SW-LOAD-4: Q4.5 (D); also elsewhere on the board

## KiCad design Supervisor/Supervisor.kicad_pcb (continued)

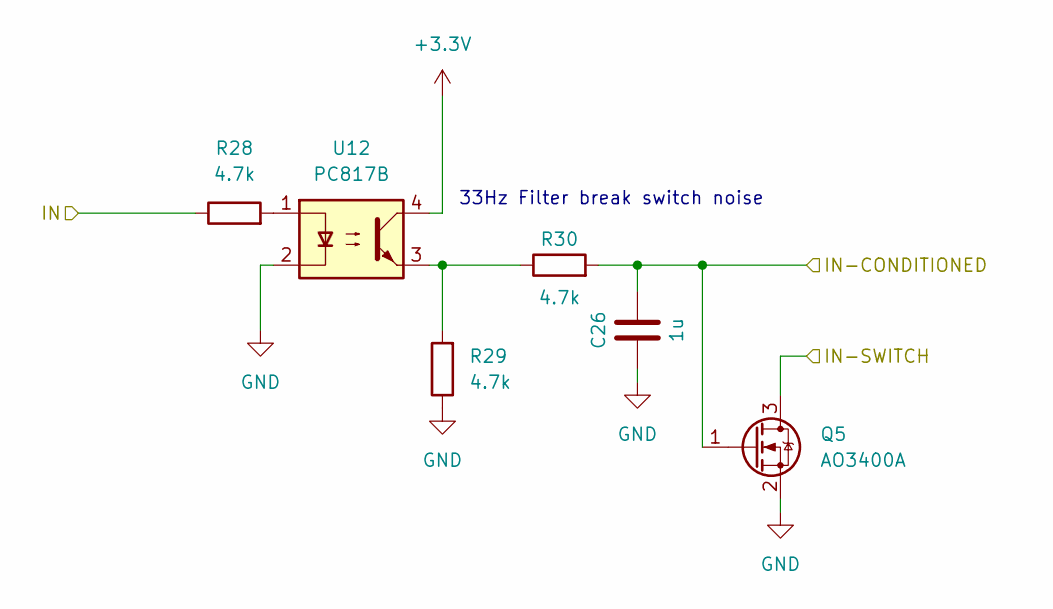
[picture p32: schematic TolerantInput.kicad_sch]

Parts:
C26: 1u; C_0603_1608Metric; MPN C15849
Q5: AO3400A; SOT-23; MPN C20917
R28, R29, R30: 4.7k; R_0603_1608Metric; MPN C23162
U12: PC817B; SMDIP-4_W7.62mm; MPN C3025163

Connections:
+3.3V: U12.4; also elsewhere on the board
D-IN-3: R28.1; also elsewhere on the board
DIGITAL-4-CLAMP: Q5.3 (D); also elsewhere on the board
GND: C26.2, Q5.2 (S), R29.1, U12.2; also elsewhere on the board
unnamed: R28.2, U12.1
unnamed: R29.2, R30.1, U12.3

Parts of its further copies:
C24: 1u; C_0603_1608Metric; MPN C15849
Q6: AO3400A; SOT-23; MPN C20917
R26, R27, R31: 4.7k; R_0603_1608Metric; MPN C23162
U13: PC817B; SMDIP-4_W7.62mm; MPN C3025163

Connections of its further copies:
+3.3V: U13.4; also elsewhere on the board
D-IN-4: R26.1; also elsewhere on the board
DIGITAL-3-CLAMP: Q6.3 (D); also elsewhere on the board
GND: C24.2, Q6.2 (S), R27.1, U13.2; also elsewhere on the board
unnamed: R26.2, U13.1
unnamed: R27.2, R31.1, U13.3

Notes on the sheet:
33Hz Filter break switch noise

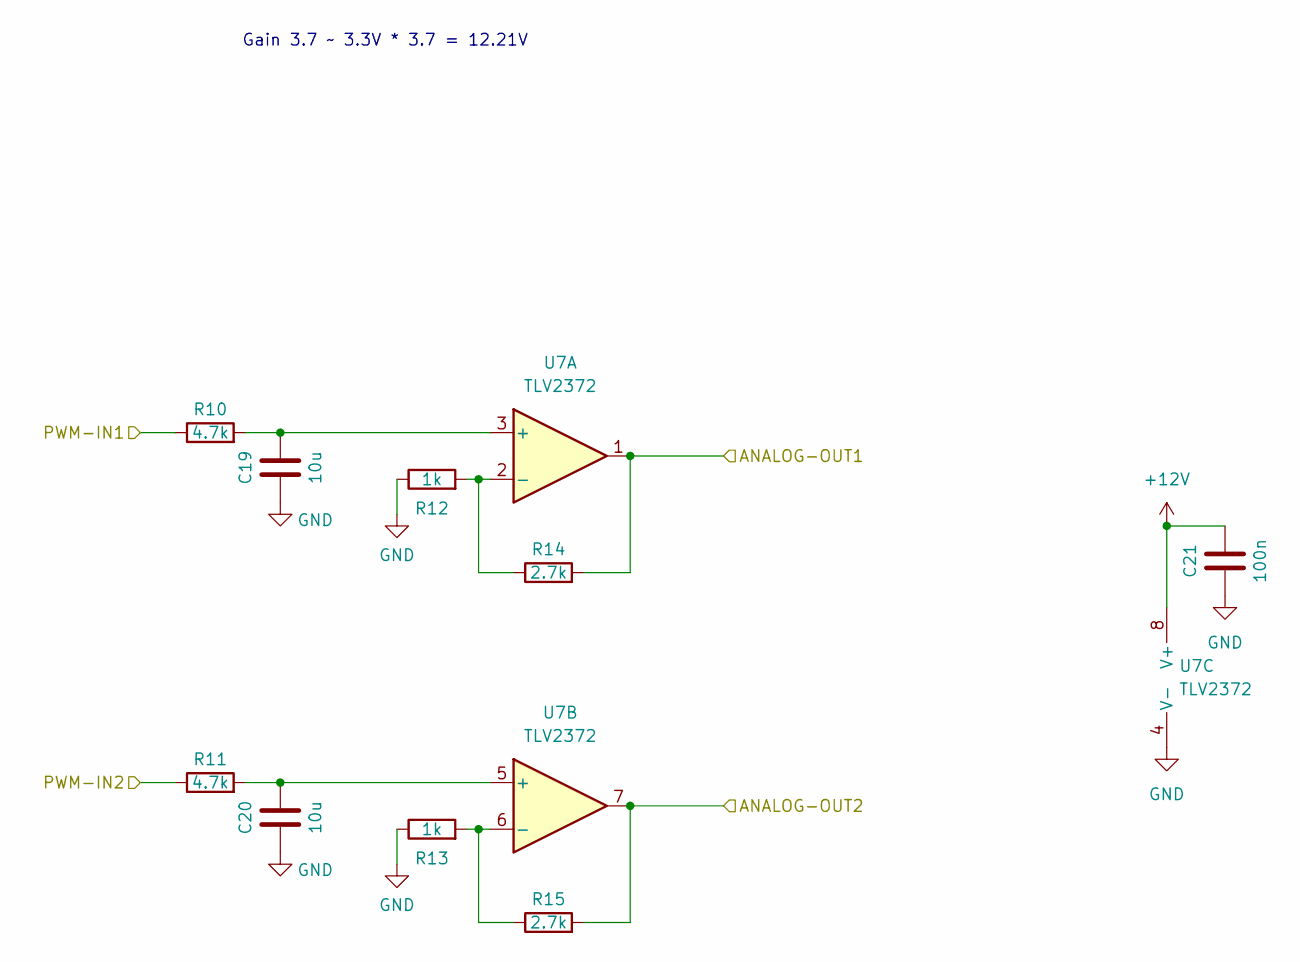
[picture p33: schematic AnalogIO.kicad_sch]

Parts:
C19, C20: 10u; C_0603_1608Metric; MPN C19702
C21: 100n; C_0603_1608Metric; MPN C14663
R10, R11: 4.7k; R_0603_1608Metric; MPN C23162
R12, R13: 1k; R_0603_1608Metric; MPN C21190
R14, R15: 2.7k; R_0603_1608Metric; MPN C13167
U7: TLV2372; SOIC-8_3.9x4.9mm_P1.27mm; MPN C27204

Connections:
+12V: C21.1, U7.8 (V+); also elsewhere on the board
AO1: R14.2, U7.1; also elsewhere on the board
AO2: R15.2, U7.7; also elsewhere on the board
GND: C19.2, C20.2, C21.2, R12.1, R13.1, U7.4 (V-); also elsewhere on the board
unnamed: C19.1, R10.2, U7.3 (+)
unnamed: R12.2, R14.1, U7.2 (-)
unnamed: C20.1, R11.2, U7.5 (+)
unnamed: R13.2, R15.1, U7.6 (-)
PWM1: R10.1; also elsewhere on the board
PWM2: R11.1; also elsewhere on the board

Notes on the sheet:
Gain 3.7 ~ 3.3V * 3.7 = 12.21V

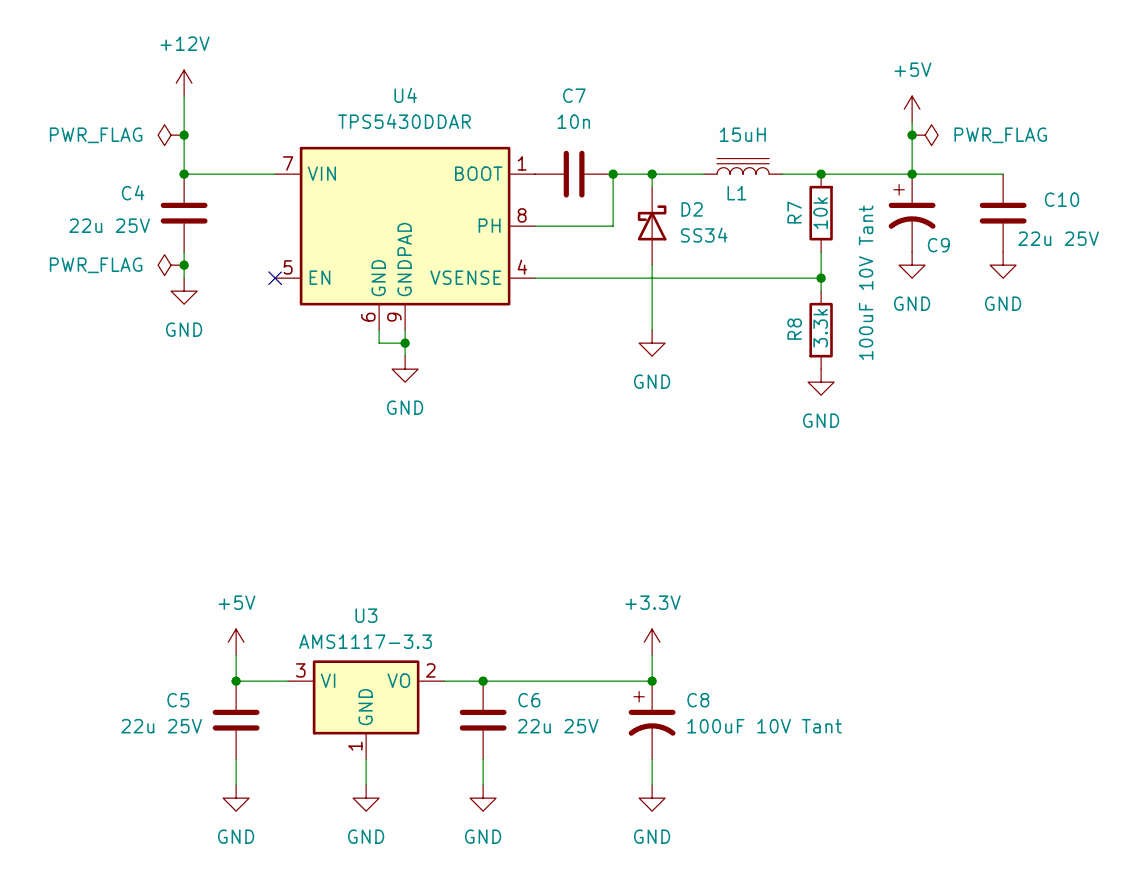
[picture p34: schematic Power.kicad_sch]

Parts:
C4, C5, C6, C10: 22u 25V; C_1206_3216Metric; MPN C12891
C7: 10n; C_0603_1608Metric; MPN C57112
C8, C9: 100uF 10V Tant; CP_EIA-6032-28_Kemet-C; MPN C171664; JLCRotOffset -180
D2: SS34; D_SMA; MPN C8678
L1: 15uH; L_Bourns_SRP7028A_7.3x6.6mm; MPN C177243
R7: 10k; R_0603_1608Metric; MPN C25804
R8: 3.3k; R_0603_1608Metric; MPN C22978
U3: AMS1117-3.3; SOT-223-3_TabPin2; MPN C6186; JLCRotOffset -180
U4: TPS5430DDAR; TI_SO-PowerPAD-8_ThermalVias; MPN C9864

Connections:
+3.3V: C6.1, C8.1, U3.2 (VO); also elsewhere on the board
+5V: C5.1, C9.1, C10.1, L1.2, R7.2, U3.3 (VI); also elsewhere on the board
+12V: C4.1, U4.7 (VIN); also elsewhere on the board
GND: C4.2, C5.2, C6.2, C8.2, C9.2, C10.2, D2.2 (A), R8.2, U3.1 (GND), U4.6 (GND), U4.9 (GNDPAD); also elsewhere on the board
unnamed: C7.1, D2.1 (K), L1.1, U4.8 (PH)
unnamed: C7.2, U4.1 (BOOT)
unnamed: R7.1, R8.1, U4.4 (VSENSE)

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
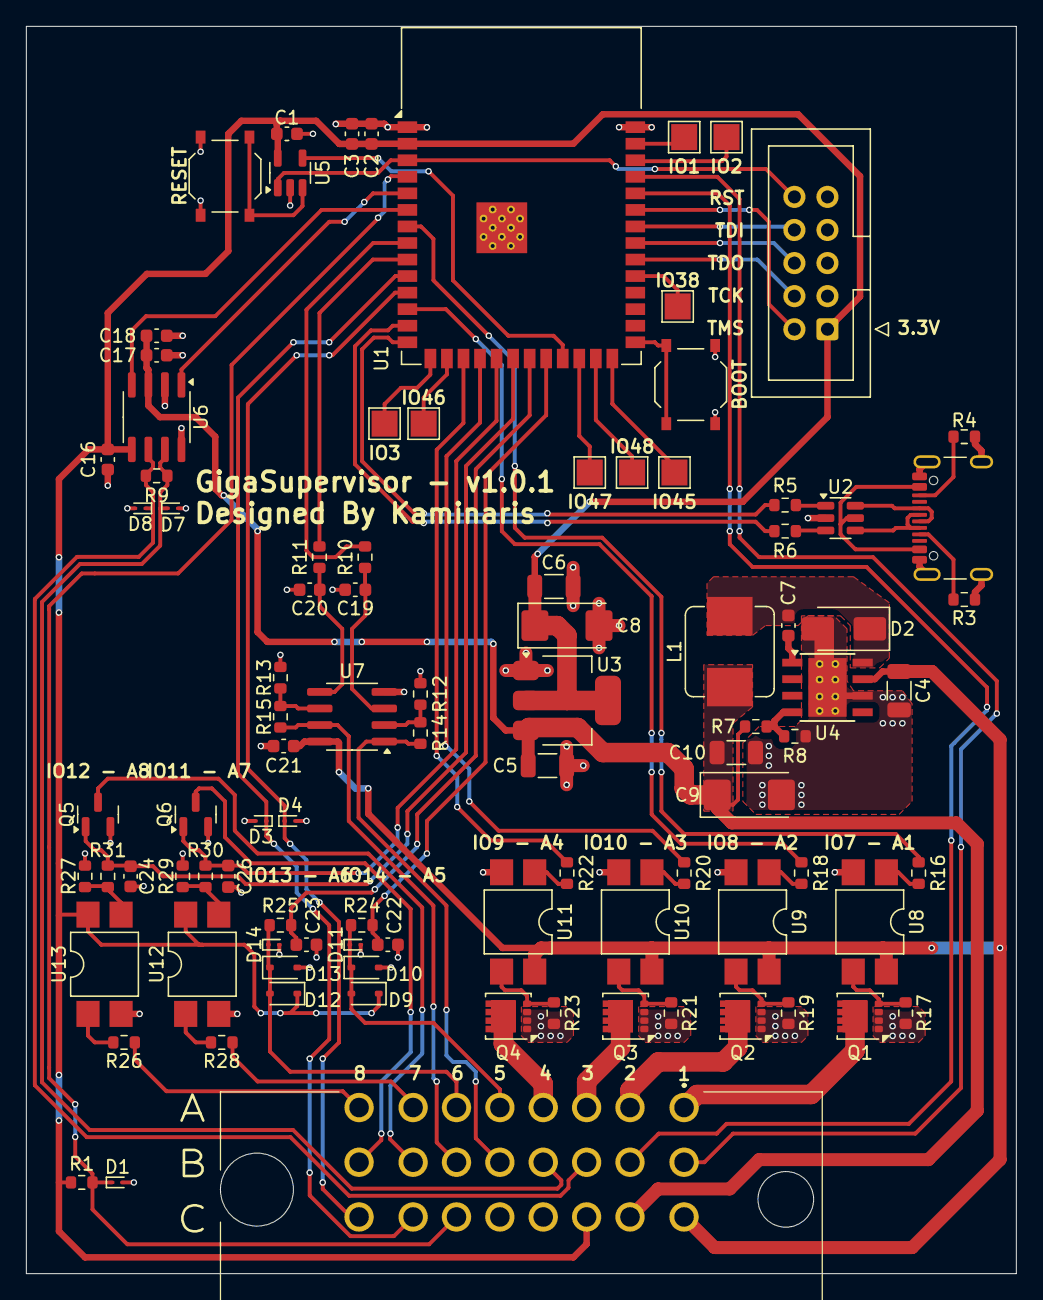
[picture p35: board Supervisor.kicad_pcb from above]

Board: 2 copper layers, 76.0 x 95.8 mm, 97 parts (0 on the bottom side), 79 nets.

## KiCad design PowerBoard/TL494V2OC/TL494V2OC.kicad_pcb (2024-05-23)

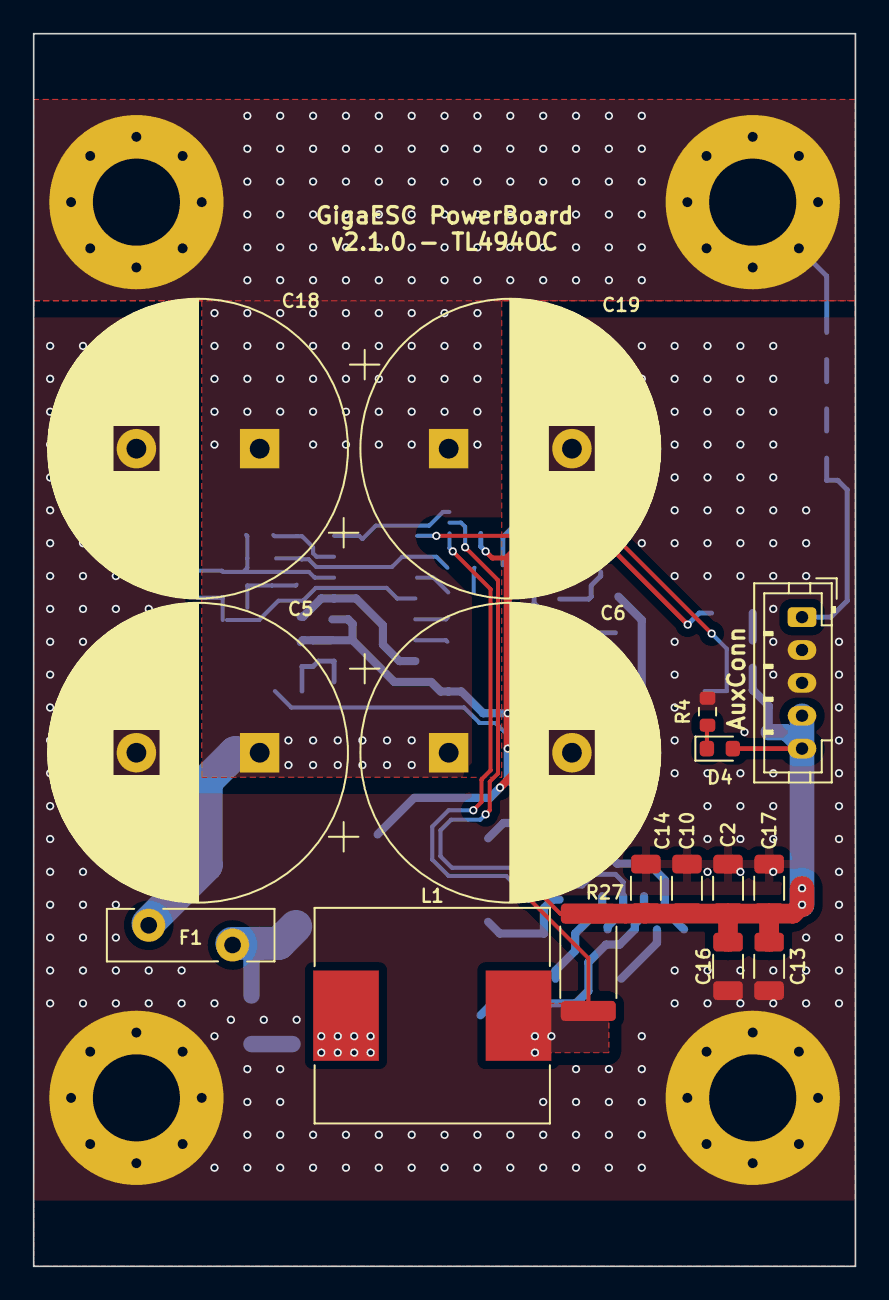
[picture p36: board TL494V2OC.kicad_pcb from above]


Board: 2 copper layers, 50.0 x 75.0 mm, 68 parts (48 on the bottom side), 34 nets.

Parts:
C1, C4, C21: 100n; C_0603_1608Metric
C2, C10, C13, C14, C16, C17: 22u; C_1206_3216Metric
C3, C8: 1n; C_0603_1608Metric
C5, C6, C18, C19: 330u 200V; CP_Radial_D18.0mm_P7.50mm
C7, C9: 2.2u 100V; C_1206_3216Metric
C11: 1u; C_0603_1608Metric
C12: 100n 200V; C_0805_2012Metric
C15: 47u 16V; C_1210_3225Metric
C20: 10u; C_0603_1608Metric
D1: SS520F; D_SMA
D2: CI04S65E3; TO-252-2
D3: BZT52C5V1S; D_SOD-323_HandSoldering
D4: RUN; D_0603_1608Metric
D5: BZG03C16-M3-08; D_SMB
D6: 1N5819WS; D_SOD-323_HandSoldering
F1: RLVR240-100; Fuse_Bourns_MF-RHT400
H1, H2, H3, H4: MountingHole_Pad; MountingHole_5.3mm_M5_Pad_Via
J1: AuxConn; JST_PH_B5B-PH-K_1x05_P2.00mm_Vertical
L1: 100uH; L_Chilisin_BMRG00131360
Q1: MMBTA92; SOT-23
Q2: CPC3980; SOT-223-3_TabPin2
Q5: IRFS4227TRLPBF; TO-263-2
R1, R24, R25: 348k; R_0603_1608Metric
R2: 18.7k; R_0603_1608Metric
R3, R16, R22: 10k; R_0603_1608Metric
R4: 82k; R_0603_1608Metric
R5: 100; R_0603_1608Metric
R6: 2k; R_0603_1608Metric
R7, R13, R26: 22; R_0603_1608Metric
R8: 1k; R_0603_1608Metric
R9, R10, R11, R12: 5.1k; R_0603_1608Metric
R14: 200k; R_0603_1608Metric
R17: 47; R_0603_1608Metric
R18: 9.1k; R_0603_1608Metric
R19: 30k; R_0603_1608Metric
R20: 100k; R_0603_1608Metric
R21: 27k; R_0603_1608Metric
R23: 4.7k; R_0603_1608Metric
R27: 10m; R_2512_6332Metric
R28: 20k; R_0603_1608Metric
U1: TL494; SOIC-16_3.9x9.9mm_P1.27mm
U2: INA213; SOT-363_SC-70-6
U3: IR2181; SOIC-8_3.9x4.9mm_P1.27mm
U4: TL431; SOT-23

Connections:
+12V: C2.1, C10.1, C13.1, C14.1, C15.1, C16.1, C17.1, D4.2 (A), J1.4, J1.5, R20.1, R26.1, R27.2, U2.5 (-)
+BATT: C5.1, C6.1, C18.1, C19.1, F1.1, H2.1, H4.1, R1.1
+VSW: C7.1, F1.2, Q2.2 (D), Q5.2 (D)
-BATT: C2.2, C3.2, C4.2, C5.2, C6.2, C9.2, C10.2, C11.2, C13.2, C14.2, C15.2, C16.2, C17.2, C18.2, C19.2, D2.3 (A), D5.2 (A), H1.1, H3.1, J1.2, J1.3, R2.2, R3.2, R4.1, R9.2, R10.2, R12.2, R18.2, R21.2, R23.2, U1.7 (GND), U1.13 (OUTCTRL), U2.1 (REF), U2.2 (GND), U3.2 (LIN), U3.3 (COM), U4.3 (A)
/SW-NODE: C12.2, D2.1 (K), D2.2 (K), L1.1, Q1.3 (C), Q5.3 (S), R8.1, U3.6 (VS)
CFB: U1.16 (2IN+), U2.6
CFB-: R9.1, R28.2, U1.15 (2IN-)
DRV-OUT: Q1.1 (B), R8.2, R13.1, U3.7 (HO)
IN_V: J1.1, R2.1, R25.2
unnamed: C1.1, R6.2
unnamed: C7.2, C9.1
unnamed: C21.2, R10.1, R11.2, R14.2
unnamed: D1.2 (A), R7.2
unnamed: C12.1, D1.1 (K), U3.8 (VB)
unnamed: D3.1 (K), R16.1, R17.2
unnamed: D4.1 (K), R4.2
unnamed: D5.1 (K), L1.2, R27.1, U2.4 (+)
unnamed: D6.2 (A), R26.2
unnamed: Q1.2 (E), Q5.1 (G), R13.2
unnamed: C8.1, Q2.1 (G), R16.2, U4.2 (K)
unnamed: Q2.3 (S), R17.1
unnamed: R1.2, R24.1
unnamed: R24.2, R25.1
unnamed: C21.1, R6.1, R14.1, U1.2 (1IN-)
unnamed: C3.1, U1.5 (CT)
unnamed: C20.2, R22.2, R23.1, U1.4 (DTC)
unnamed: R3.1, R5.2, U1.9 (E1), U1.10 (E2)
unnamed: C1.2, U1.3 (FB)
unnamed: C20.1, R11.1, R22.1, R28.1, U1.14 (REF)
unnamed: R12.1, U1.6 (RT)
unnamed: R5.1, U3.1 (HIN)
unnamed: C8.2, R18.1, R19.1, U4.1 (R)
STARTUP: C4.1, C11.1, D3.2 (A), D6.1 (K), R7.1, R19.2, U1.8 (C1), U1.11 (C2), U1.12 (VCC), U2.3 (V+), U3.5 (VCC)
VFB: R20.2, R21.1, U1.1 (1IN+)

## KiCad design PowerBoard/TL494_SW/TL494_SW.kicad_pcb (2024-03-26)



Board: 2 copper layers, 50.0 x 75.0 mm, 69 parts (50 on the bottom side), 36 nets.

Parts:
C1, C4, C20: 100n; C_0603_1608Metric
C2, C10, C13, C14, C16, C17: 22u; C_1206_3216Metric
C3, C8: 1n; C_0603_1608Metric
C5, C6, C18, C19: 330u 200V; CP_Radial_D18.0mm_P7.50mm
C7, C9: 2.2u 100V; C_1206_3216Metric
C11: 1u; C_0603_1608Metric
C12: 220n; C_1206_3216Metric
C15: 47u 16V; C_1210_3225Metric
D1, D2: SS520F; D_SMA
D3: BZT52C5V1S; D_SOD-323_HandSoldering
D4: RUN; D_0603_1608Metric
D5: 3SMB5928B; D_SMB
D6: 1N5819WS; D_SOD-323_HandSoldering
F1: Fuse; Fuse_2512_6332Metric_Pad1.52x3.35mm_HandSolder
H1, H2, H3, H4: MountingHole_Pad; MountingHole_5.3mm_M5_Pad_Via
J1: AuxConn; JST_PH_B5B-PH-K_1x05_P2.00mm_Vertical
J2: POWER_SW; JST_PH_B4B-PH-K_1x04_P2.00mm_Vertical
L1: 100uH; L_Chilisin_BMRG00131360
Q1: MMBTA42; SOT-23
Q2: BSS126; SOT-23
Q3: IRF9640SPBF; TO-263-2
Q4: S9012 2T1; SOT-23
Q5: IRFS4227TRLPBF; TO-263-2
R1: 150k; R_0603_1608Metric
R2, R21: 2.7k; R_0603_1608Metric
R3, R15, R16, R18, R20: 10k; R_0603_1608Metric
R4: 82k; R_0603_1608Metric
R5, R9, R17: 100; R_0603_1608Metric
R6: 2k; R_0603_1608Metric
R7, R13: 22; R_0603_1608Metric
R10, R11, R12: 5.1k; R_0603_1608Metric
R14, R25: 200k; R_0603_1608Metric
R19: 30k; R_0603_1608Metric
R24, R27: 100k; R_0603_1608Metric
R26: 20k; R_0603_1608Metric
R28: 27k; R_0603_1608Metric
R29: 1k; R_0603_1608Metric
TP1: TestPoint; TestPoint_Pad_1.0x1.0mm
U1: TL494; SOIC-16_3.9x9.9mm_P1.27mm
U3: IRS21271; SO-8_3.9x4.9mm_P1.27mm
U4: TL431; SOT-23

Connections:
+12V: C2.1, C10.1, C13.1, C14.1, C15.1, C16.1, C17.1, D4.2 (A), D5.1 (K), D6.2 (A), J1.4, J1.5, L1.2, R20.2
+BATT: C5.1, C6.1, C18.1, C19.1, F1.1, H2.1, H4.1, R1.1
+VSW: C7.1, Q2.3 (D), Q3.2 (D), Q5.2 (D), R24.2
-BATT: C2.2, C3.2, C4.2, C5.2, C6.2, C9.2, C10.2, C11.2, C13.2, C14.2, C15.2, C16.2, C17.2, C18.2, C19.2, D2.2 (A), D5.2 (A), H1.1, H3.1, J1.2, J1.3, J2.1, R2.2, R3.2, R4.1, R9.1, R10.2, R12.2, R18.1, R21.1, R26.2, R28.2, U1.4 (DTC), U1.7 (GND), U1.13 (OUTCTRL), U3.4 (COM), U4.3 (A)
BOOTSTRAP: C4.1, C11.1, D3.2 (A), D6.1 (K), R7.1, R19.2, U1.8 (C1), U1.11 (C2), U1.12 (VCC), U3.1 (VCC)
IN_V: J1.1, R1.2, R2.1
unnamed: C1.1, R6.2
unnamed: C7.2, C9.1
unnamed: D1.2 (A), R7.2
unnamed: C12.1, D1.1 (K), U3.8 (VB)
unnamed: C12.2, D2.1 (K), L1.1, Q4.3 (C), Q5.3 (S), R29.1, U3.5 (VS), U3.6 (CS)
unnamed: D3.1 (K), R16.1, R17.1
unnamed: D4.1 (K), R4.2
unnamed: J2.2, R24.1
unnamed: J2.3, R25.2
unnamed: J2.4, Q1.1 (B), R26.1
unnamed: C20.2, Q1.3 (C), Q3.1 (G), R27.2
unnamed: Q1.2 (E), R28.1
unnamed: C8.1, Q2.1 (G), R16.2, U4.2 (K)
unnamed: Q2.2 (S), R17.2
unnamed: C20.1, F1.2, Q3.3 (S), R25.1, R27.1
unnamed: Q4.1 (B), R13.1, R29.2, U3.7 (HO)
unnamed: Q4.2 (E), Q5.1 (G), R13.2
unnamed: R10.1, R11.2, R14.2
unnamed: R6.1, R14.1, U1.2 (1IN-)
unnamed: R9.2, U1.16 (2IN+)
unnamed: R15.2, U1.15 (2IN-)
unnamed: C3.1, U1.5 (CT)
unnamed: R3.1, R5.2, U1.9 (E1), U1.10 (E2)
unnamed: C1.2, R15.1, U1.3 (FB)
unnamed: R11.1, U1.14 (REF)
unnamed: R12.1, U1.6 (RT)
unnamed: TP1.1, U3.3 (FAULT)
unnamed: R5.1, U3.2 (IN)
unnamed: C8.2, R18.2, R19.1, U4.1 (R)
VFB: R20.1, R21.2, U1.1 (1IN+)

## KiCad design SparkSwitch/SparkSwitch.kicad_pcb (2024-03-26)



Board: 2 copper layers, 100.0 x 70.0 mm, 27 parts (4 on the bottom side), 18 nets.

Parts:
C1: 1u; C_0603_1608Metric
D1, D2: BZT52B12; D_SOD-123F
J3: POWER_SW; JST_PH_B4B-PH-K_1x04_P2.00mm_Vertical
J5: NegativeIn; MountingHole_5.3mm_M5_Pad_Via
J7: NegativeOut; MountingHole_5.3mm_M5_Pad_Via
Q1, Q2, Q3, Q4: IRF200P222; TO-247-3_Horizontal_TabDown
R2: 10k; R_0603_1608Metric
R3, R11, R12, R13, R14, R15, R16: 100k; R_0603_1608Metric
R4, R17: 1k; R_0603_1608Metric
R6, R7, R8, R9, R10: 22; R_0603_1608Metric
TP1: TestPoint; TestPoint_Pad_1.0x1.0mm
U1: LTV-352T; SO-4_4.4x3.6mm_P2.54mm

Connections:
+VSW: R3.2, R14.1, R17.1
-BATT: J3.1, J7.1, Q1.2 (D), Q2.2 (D), Q3.2 (D), Q4.2 (D), R4.2
GND: D1.2 (A), D2.2 (A), J5.1, Q1.1 (S), Q2.1 (S), Q3.1 (S), Q4.1 (S), R2.2, R11.2, U1.2
unnamed: C1.1, R4.1
unnamed: C1.2, D1.1 (K), R2.1, R6.2, R7.2, R8.2, R9.2, U1.3
unnamed: J3.2, R3.1
unnamed: Q1.3 (G), R6.1
unnamed: Q2.3 (G), R7.1
unnamed: Q3.3 (G), R8.1
unnamed: Q4.3 (G), R9.1
unnamed: R10.2, U1.1
unnamed: R11.1, R12.2
unnamed: R12.1, R13.2
unnamed: R14.2, R15.1
unnamed: R15.2, R16.1
unnamed: R17.2, U1.4
SW_NC: J3.4, R10.1
SW_NX: D2.1 (K), J3.3, R13.1, R16.2

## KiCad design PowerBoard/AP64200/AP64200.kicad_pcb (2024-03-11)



Board: 2 copper layers, 50.0 x 75.0 mm, 52 parts (36 on the bottom side), 28 nets.

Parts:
C1, C15: 100n; C_0603_1608Metric
C2, C10, C13, C14, C16: 22u; C_1206_3216Metric
C5, C6, C18, C19: 330u 200V; CP_Radial_D18.0mm_P7.50mm
C7, C9: 2.2u 100V; C_1206_3216Metric
C11: 1u; C_0603_1608Metric
C21: 22n; C_0603_1608Metric_L
C22: 10u; C_0805_2012Metric
D2: SS520F; D_SMA
D7, D9: BZT52C8V2S; D_SOD-323_HandSoldering
D8: BZT52B12; D_SOD-123F
H1, H2, H3, H4: MountingHole_Pad; MountingHole_5.3mm_M5_Pad_Via
J1: AuxConn; JST_PH_B5B-PH-K_1x05_P2.00mm_Vertical
J2: POWER_SW; JST_PH_B4B-PH-K_1x04_P2.00mm_Vertical
L1: 100uH; L_Chilisin_BMRG00131360
Q3: IRF9640SPBF; TO-263-2
Q4, Q6, Q8: S9012 2T1; SOT-23
Q7, Q10: MMBTA42; SOT-23
Q9: MMBTA92T; SOT-89-3
R1: 150k; R_0603_1608Metric
R2: 2.7k; R_0603_1608Metric
R3: 22; R_0603_1608Metric
R8, R29: 1k; R_0603_1608Metric
R15, R33: 10k; R_0603_1608Metric
R22, R32: 820; R_0603_1608Metric
R23: 220k; R_0603_1608Metric
R24, R30, R31, R37: 100k; R_0603_1608Metric
R34: 150; R_0603_1608Metric
R35: 4.7k; R_0603_1608Metric
R36: 30k; R_0603_1608Metric
U5: LT8609AJDDM; DFN-10-1EP_2.6x2.6mm_P0.5mm_EP1.3x2.2mm

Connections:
+12V: C2.1, C10.1, C13.1, C14.1, C16.1, J1.4, J1.5, L1.2, Q7.1 (B), R24.2
+BATT: C5.1, C6.1, C7.1, C18.1, C19.1, C22.1, D7.1 (K), D8.1 (K), H2.1, H4.1, R1.1, R8.2, R29.2, R30.1, U5.9 (VIN)
-BATT: C2.2, C5.2, C6.2, C9.2, C10.2, C13.2, C14.2, C15.1, C16.2, C18.2, C19.2, C21.2, D2.2 (A), D9.2 (A), H1.1, H3.1, J1.2, J1.3, J2.1, Q9.2 (C), R2.2, R15.1, R35.2
GNDH: C11.2, C22.2, Q8.3 (E), R3.2, R22.1, R23.2, R33.1, R34.1, U5.11 (GND)
IN_V: J1.1, R1.2, R2.1
unnamed: C7.2, C9.1
unnamed: C21.1, R32.1
unnamed: D2.1 (K), L1.1, Q3.2 (D)
unnamed: D7.2 (A), R33.2, U5.10 (EN/UV)
unnamed: D8.2 (A), Q8.2 (C), Q9.1 (B), Q10.3 (C)
unnamed: C15.2, D9.1 (K), J2.4, R36.1
unnamed: J2.2, R24.1
unnamed: J2.3, R37.2
unnamed: Q3.1 (G), R3.1
unnamed: C1.1, Q3.3 (S), U5.2 (SW)
unnamed: Q4.1 (B), Q6.1 (B), Q6.2 (C), Q7.3 (C)
unnamed: Q4.2 (C), R22.2, U5.6 (FB)
unnamed: Q4.3 (E), R8.1
unnamed: Q6.3 (E), R29.1
unnamed: Q7.2 (E), R15.2, R32.2
unnamed: Q8.1 (B), Q9.3 (E), R34.2
unnamed: Q10.1 (B), R36.2
unnamed: Q10.2 (E), R35.1
unnamed: R30.2, R31.1
unnamed: R31.2, R37.1
unnamed: C1.2, U5.1 (BST)
unnamed: C11.1, U5.3 (INTVCC)
unnamed: R23.1, U5.4 (RT)

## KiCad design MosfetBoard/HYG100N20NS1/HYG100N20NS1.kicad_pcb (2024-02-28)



Board: 2 copper layers, 100.0 x 75.0 mm, 88 parts (21 on the bottom side), 55 nets, no tracks yet.

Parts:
C1, C2, C3, C4, C8, C9, C10, C11, C25, C26, C27, C28, C30, C31, C32, C33, C48, C49, C50, C51, C52, C53, C54, C55: 10u 100V; C_1210_3225Metric
C5, C12, C15: 100n; C_0603_1608Metric
C6, C13, C16: 10n; C_0603_1608Metric
C7, C14, C17: 1n; C_0603_1608Metric
C18, C19, C20: 1u; C_0603_1608Metric
H1, H2, H3, H4, H5: MountingHole_Pad; MountingHole_5.3mm_M5_Pad_Via
H6, H7, H8, H9: MountingHole; MountingHole_3.2mm_M3_ISO14580
J1: LogicConnector; PinSocket_2x15_P2.54mm_Vertical
Q1, Q2, Q3, Q4, Q5, Q6, Q7, Q8, Q9, Q10, Q11, Q12: HYG100N20NS1; TO-220-3_Horizontal_TabUp
R1, R2, R3: 10k; R_0603_1608Metric
R5, R6, R7, R8, R9, R10, R11, R12, R16, R17, R18, R19: 2.2; R_0603_1608Metric
R22, R25, R28: 0.3m; R_2512_6332Metric
R23, R26, R29: 4.7k; R_0603_1608Metric
R24, R27, R30: 9.1k; R_0603_1608Metric
TH1, TH2, TH3: NCP18XH103F03RB; R_0603_1608Metric
U4, U8, U9: MT9223CT-50BR5; SOP-8_3.9x4.9mm_P1.27mm

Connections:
+BATT: C1.1, C8.1, C10.1, C25.1, C26.1, C28.1, C31.1, C33.1, C48.1, C50.1, C52.1, C54.1, H5.1, Q1.2 (D), Q3.2 (D), Q5.2 (D), Q7.2 (D), Q9.2 (D), Q11.2 (D)
-BATT: C2.2, C3.2, C4.2, C9.2, C11.2, C18.2, C19.2, C20.2, C27.2, C30.2, C32.2, C49.2, C51.2, C53.2, C55.2, H4.1, J1.12, J1.20, J1.28, J1.29, J1.30, Q2.3 (S), Q4.3 (S), Q6.3 (S), Q8.3 (S), Q10.3 (S), Q12.3 (S), R1.2, R2.2, R3.2
/3.3V: J1.2, TH1.1, TH2.1, TH3.1
/5V: C5.2, C12.2, C15.2, J1.4, U4.8 (VCC), U8.8 (VCC), U9.8 (VCC)
/PH1: J1.6, R9.1, R11.1
/PH2: J1.14, R5.1, R7.1
/PH3: J1.22, R16.1, R18.1
/PHASE1: J1.8, Q1.3 (S), Q2.2 (D), Q3.3 (S), Q4.2 (D), R22.2, U4.1 (IP+), U4.2 (IP+)
/PHASE2: J1.16, Q5.3 (S), Q6.2 (D), Q7.3 (S), Q8.2 (D), R25.2, U8.1 (IP+), U8.2 (IP+)
/PHASE3: J1.24, Q9.3 (S), Q10.2 (D), Q11.3 (S), Q12.2 (D), R28.2, U9.1 (IP+), U9.2 (IP+)
/PL1: J1.10, R10.1, R12.1
/PL2: J1.18, R6.1, R8.1
/PL3: J1.26, R17.1, R19.1
/PhaseMosfets1/MOS_TEMP: C18.1, J1.5, R1.1, TH1.2
/PhaseMosfets1/PHASE_OUT: H1.1, R22.1, U4.3 (IP-), U4.4 (IP-)
/PhaseMosfets1/SH+: J1.11, R23.1, R24.2
/PhaseMosfets1/SH-: C5.1, C6.2, C7.2, J1.9, R24.1, U4.5 (GND)
/PhaseMosfets2/MOS_TEMP: C19.1, J1.13, R2.1, TH2.2
/PhaseMosfets2/PHASE_OUT: H2.1, R25.1, U8.3 (IP-), U8.4 (IP-)
/PhaseMosfets2/SH+: J1.19, R26.1, R27.2
/PhaseMosfets2/SH-: C12.1, C13.2, C14.2, J1.17, R27.1, U8.5 (GND)
/PhaseMosfets3/MOS_TEMP: C20.1, J1.21, R3.1, TH3.2
/PhaseMosfets3/PHASE_OUT: H3.1, R28.1, U9.3 (IP-), U9.4 (IP-)
/PhaseMosfets3/SH+: J1.27, R29.1, R30.2
/PhaseMosfets3/SH-: C15.1, C16.2, C17.2, J1.25, R30.1, U9.5 (GND)
unnamed: C1.2, C2.1
unnamed: C4.1, C48.2
unnamed: C8.2, C9.1
unnamed: C10.2, C11.1
unnamed: C3.1, C25.2
unnamed: C26.2, C27.1
unnamed: C28.2, C30.1
unnamed: C31.2, C32.1
unnamed: C33.2, C49.1
unnamed: C50.2, C51.1
unnamed: C52.2, C53.1
unnamed: C54.2, C55.1
unnamed: Q1.1 (G), R9.2
unnamed: Q2.1 (G), R10.2
unnamed: Q3.1 (G), R11.2
unnamed: Q4.1 (G), R12.2
unnamed: Q5.1 (G), R5.2
unnamed: Q6.1 (G), R6.2
unnamed: Q7.1 (G), R7.2
unnamed: Q8.1 (G), R8.2
unnamed: Q9.1 (G), R16.2
unnamed: Q10.1 (G), R17.2
unnamed: Q11.1 (G), R18.2
unnamed: Q12.1 (G), R19.2
unnamed: C6.1, U4.6 (FILTER)
unnamed: C7.1, R23.2, U4.7 (VIOUT)
unnamed: C13.1, U8.6 (FILTER)
unnamed: C14.1, R26.2, U8.7 (VIOUT)
unnamed: C16.1, U9.6 (FILTER)
unnamed: C17.1, R29.2, U9.7 (VIOUT)

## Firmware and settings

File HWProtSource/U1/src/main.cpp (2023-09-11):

/*
  created  27 Jun 2023
  by Euan Mutch (TechAUmNu)
*/

#include <Arduino.h>
#include <Comparator.h>
#include <Event.h>
#include <Logic.h>
#include <Wire.h>

#define wdtReset() __asm__ __volatile__ ("wdr"::)

#define IS_TEST_MODE
#define IS_HIGH_SIDE
#define HAS_I2C

#define POT_A_ADDRESS 0x2E    // 0b0101110
#define POT_B_ADDRESS 0x3E    // 0b0111110

#define POT_ADDRESS POT_B_ADDRESS

#define LOW_SIDE_SETTING (127 - 5)
#define HIGH_SIDE_SETTING 5

#define POT_SETTING LOW_SIDE_SETTING

void setPotValue(uint8_t addr, uint8_t value) {
	wdtReset();
	delay(100);
	Wire.beginTransmission(addr);
	Wire.write(0x00);         // sends instruction.  0x00 = Write
	Wire.write(value);         // sends value 0 = 10K, 127 = 0K
	auto res = Wire.endTransmission();     // end transmission
	Serial.printf("i2c res: %d\n", res);
	delay(100);
	wdtReset();
}

void setup() {
	// disabled
	#ifdef IS_TEST_MODE
	pinMode(PIN_PA4, OUTPUT);
	digitalWrite(PIN_PA4, LOW);
	#else
	_PROTECTED_WRITE(WDT.CTRLA, WDT_PERIOD_1KCLK_gc);

	Serial.begin(115200);
	while (!Serial) {
		wdtReset();
		delay(1);
	}
	Serial.printf("Started at %d MHz\n", F_CPU);

	// Configure event channel for reset from GPIO pin PB2
	Event1.set_generator(0xFF);
	Event1.set_user(user::ccl1_event_a);
	Event1.start();

	// Initialize logic block 1
	Logic1.enable = true;                 // Enable logic block 1
	Logic1.input0 = logic::in::event_a;     // Connect input 0 to ccl1_event_a (PB2 through Event1)
	Logic1.input1 = logic::in::masked;
	Logic1.input2 = logic::in::masked;
	Logic1.output = logic::out::disable;
	Logic1.truth = 0xFE;  // Set truth table
	Logic1.init();

	// Configure relevant comparator parameters
	Comparator0.input_p = comparator::in_p::in2;  // Use positive input 2 (PB1)
	Comparator1.input_p = comparator::in_p::in3;  // Use positive input 3 (PB4)
	Comparator2.input_p = comparator::in_p::in1;  // Use positive input 1 (PB0)

	// Initialize comparators
	Comparator0.init();
	Comparator1.init();
	Comparator2.init();

	// Configure logic block
	Logic0.enable = true;
	Logic0.input0 = logic::in::ac0;
	Logic0.input1 = logic::in::ac1;
	Logic0.input2 = logic::in::ac2;
	Logic0.output = logic::out::enable;
	Logic0.filter = logic::filter::filter;
	Logic0.sequencer = logic::sequencer::rs_latch;    // Latch output
	Logic0.truth = 0xFE;                            // Set truth table (3 input OR)
	Logic0.init();

	// Start comparators
	Comparator0.start();
	Comparator1.start();
	Comparator2.start();

	// Start the AVR logic hardware
	Logic::start();

		#ifdef HAS_I2C
	Wire.swap(1);
	Wire.begin();
	// A is connected to HIGH side, B to LOW side

	setPotValue(POT_ADDRESS, POT_SETTING);

		#endif
	analogReference(EXTERNAL); // PA5
	analogClockSpeed(-1);
	#endif
}

void loop() {
	wdtReset();

	delay(500);
	Serial.println("ping");
}

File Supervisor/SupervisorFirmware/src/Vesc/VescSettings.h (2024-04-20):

#ifndef UNIVESCDISPLAY2_VESCSETTINGS_H
#define UNIVESCDISPLAY2_VESCSETTINGS_H
#include <Arduino.h>

struct VescSettings {
	float wheelDiameter = 0.5;
	float maxBatteryVoltage = 84;
	float minBatteryVoltage = 60;
	float motorPolePairs = 30;
	float maxSpeed = 0;
	float odo = 0;
	float motorPulley = 1.0;
	float wheelPulley = 1.0;
	float maxMotorCurrent = 35.0;
	float dutyWarning = 80.0; // will play beep.mp3
	float motorTempWarning = 80.0; // will play motortemp.mp3
	float mosfetTempWarning = 80.0; // will play mosfettemp.mp3
	float speedWarning = 40.0; // will play speed.mp3
	float warningFrequency = 5.0; // each warning can only occur once per X seconds
};

#endif

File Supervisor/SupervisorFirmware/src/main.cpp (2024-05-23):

#include <LittleFS.h>
#include <BluetoothConnectivity/Plugins/ChipInfoBlePlugin.h>
#include <BluetoothConnectivity/Plugins/FileSystemBlePlugin.h>
#include <BluetoothConnectivity/Plugins/FirmwareUpdateBlePlugin.h>
#include <BluetoothConnectivity/Plugins/PreferencesBlePlugin.h>

#include "Arduino.h"
#include "BluetoothConnectivity/UniversalBleServer.h"
// #include <VescUart.h>
// #include <CanBus/CanBus.h>

constexpr gpio_num_t CAN_TX = GPIO_NUM_5;
constexpr gpio_num_t CAN_RX = GPIO_NUM_6;

PreferencesExt preferences;
// VescUart vescUart;
UniversalBleServer uniBle;
ChipInfoBlePlugin chipInfoBlePlugin(&uniBle);
FileSystemBlePlugin fileSystemBlePlugin(&uniBle);
FirmwareUpdateBlePlugin firmwareUpdateBlePlugin(&uniBle);
PreferencesBlePlugin preferencesBlePlugin(&uniBle, &preferences);

bool handleBlePacket(uint8_t packetType, uint8_t* data) {
	return false;
}

void setup() {
	Serial.begin(115200);
	Serial.println("oi");

	if (!LittleFS.begin(true)) {
		Serial.println("LittleFS Mount Failed");
		return;
	}

	// delay(1000);
	preferences.begin("supervisor", false);
	uniBle.addPlugin(&chipInfoBlePlugin);
	uniBle.addPlugin(&preferencesBlePlugin);
	uniBle.addPlugin(&fileSystemBlePlugin);
	uniBle.addPlugin(&firmwareUpdateBlePlugin);

	uniBle.setup(
		"GigaSupervisor",
		0x4B2DF921u,
		0x9086u,
		0x4977u,
		0xA30366BA8A5EB947u
	);
	uniBle.registerPacketCallback(handleBlePacket);

	// if (CanBus::setup(CAN_TX, CAN_RX)) {
	// 	Serial.println("CAN bus started!");
	// } else {
	// 	Serial.println("CAN bus failed!");
	// }

	// vescUart.setSerialPort(&Serial1);
}

void loop() {
	delay(5000);
	// vescUart.printVescValues();
	uniBle.println("ping5");
}

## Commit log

2023-06-29 fixes, led R
    [DriverSocket.kicad_sch, GigaVesc.kicad_pcb, GigaVesc.kicad_sch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]
2023-07-19 small fixes
    [DevKit.kicad_pcb, HardwareProtection.kicad_sch, Switches.kicad_sch]
2023-07-24 moved libs and gigamax version
    [ATTinyComp.kicad_sch, DriverSocket.kicad_sch, ESP32BT.kicad_sch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]
2023-07-30 small changes for lt
    [LT8316.kicad_pcb, LT8316.kicad_sch]
2023-07-30 ucc fixes
    [UCC28C45.kicad_pcb, UCC28C45.kicad_sch]
2023-08-06 fixes to caps
    [UCC21520DWR.kicad_pcb, UCC21520DWR.kicad_sch]
2023-08-06 fixes to caps and resistors on UCC21520DWR
    [UCC21520DWR.kicad_pcb, UCC21520DWR.kicad_sch]
2023-08-08 v2.4 - INA4181A1IPWR
    [ATTinyComp.kicad_sch, DevKit.kicad_pcb, DevKit.kicad_sch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]
2023-08-08 v2.5 - routed
    [DevKit.kicad_pcb]
2023-08-09 small changes
    [DevKit.kicad_pcb, IPB072N15N3G_SHUNTS.kicad_pcb, PhaseMosfets.kicad_sch]
2023-08-11 v2.6.0 - cleanup
    [DevKit.kicad_pcb, Unnamed-IXTT220N20X4HV.iges, Unnamed-IXTT220N20X4HV.obj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]
2023-08-12 v2.6.1 - EPC2304
    [DevKit.kicad_pcb, DriverSocket.kicad_sch, EPC2304.kicad_pcb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]
2023-08-12 v2.6.2 - EPC2304
    [EPC2304.kicad_pcb, PhaseMosfets.kicad_sch]
2023-08-13 v2.7.0 - Phase shunts
    [DevKit.kicad_pcb, DevKit.kicad_sch, EPC2304.kicad_pcb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]
2023-08-14 v2.8.0 - Small Hall sensors
    [ATTinyComp.kicad_sch, Barebone.kicad_pcb, Barebone.kicad_sch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]
2023-08-15 v2.9.0 - Small Hall/low side shunt
    [LowSideShuntAmp.kicad_sch, logicconnectors.kicad_sch]
2023-08-15 v2.10.0 - Low side shunt and hall sensor
    [DevKit.kicad_pcb, DevKit.kicad_sch, ShuntAmp.kicad_sch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]
2023-08-15 v2.10.0 - Low side shunt and hall sensor - logic routed
    [DevKit.kicad_pcb, DriverSocket.kicad_sch, EPC2304.kicad_pcb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]
2023-08-15 v2.10.0 - Low side shunt and hall sensor - current filters
    [ATTinyComp.kicad_sch, DevKit.kicad_pcb, DevKit.kicad_sch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]
2023-08-16 v2.10.0 - Low side shunt and hall sensor - epc routed
    [EPC2304.kicad_pcb, PhaseMosfets.kicad_sch]
2023-08-16 v2.10.0 - Low side shunt and hall sensor - epc finished
    [DevKit.kicad_pcb, EPC2304.kicad_pcb, IPB072N15N3G_SHUNTS.kicad_pcb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]
2023-08-16 v2.10.0 - Release
    [DevKit.kicad_pcb, EPC2304.kicad_pcb, UCC28C45.kicad_pcb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]
2023-09-11 v2.10.1 - GaN Working
    [EPC2304.kicad_pcb, IPB072N15N3G_SHUNTS.kicad_pcb, UCC28C45.kicad_pcb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]
2023-09-15 v3.0.0 - GaN redesign begin
    [DevKit.kicad_pcb, DevKit.kicad_sch, DriverSocket.kicad_sch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]
2023-11-25 v3.0.1 - GaN redesign
    [DIGITAL.kicad_pcb, DIGITAL.kicad_sch, DevKit.kicad_pcb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]
2023-11-25 v3.0.1 - Readme fix
    [UCC28C45_old.kicad_pcb, UCC28C45_old.kicad_sch]
2023-11-25 v3.0.1 - Devkit rerouted
    [DevKit.kicad_pcb, TL494.kicad_sch]
2023-11-26 v3.0.2 - IPB v2
    [DevKit.kicad_pcb, EPC2304.kicad_pcb, IPB072N15N3G.kicad_pcb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]
2023-11-29 v3.0.2 - Prerelease
    [DevKit.kicad_pcb, DevKit.kicad_sch, DriverSocket.kicad_sch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]
2024-01-21 v3.0.3 - Cosmetic Changes
    [DIGITAL.kicad_pcb, DevKit.kicad_pcb, DriverSocket.kicad_sch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]
2024-02-22 v3.0.4 - EPC resistor changes
    [EPC2304.kicad_pcb, PhaseMosfets.kicad_sch]
2024-02-28 v3.1.0 - Power supply fixes
    [LT8609A.kicad_pcb, LT8609A.kicad_sch, SparkSwitch.kicad_pcb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]
2024-02-28 v3.1.1 - TO220 mosfets
    [HYG100N20NS1.kicad_pcb, HYG100N20NS1.kicad_sch, PhaseMosfets.kicad_sch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]
2024-03-11 v3.2.0 - Moving to kicad 8
    [ATTinyComp.kicad_sch, DevKit.kicad_pcb, DevKit.kicad_sch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]
2024-03-26 v3.2.2 - TL494V2
    [AP64200.kicad_pcb, AP64200.kicad_sch, ATTinyComp.kicad_sch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]
2024-04-20 v3.3.0 - TL494V2
    [TL494V2.kicad_pcb, TL494V2.kicad_sch]
2024-04-26 v3.3.1 - Supervisor routed
    [AnalogIO.kicad_sch, ESC.kicad_sch, HCCPHPE24BKA90F.stp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]
2024-05-07 Supervisor FW
    [AnalogIO.kicad_sch, ESC.kicad_sch, InputProtection.kicad_sch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]
2024-05-23 EPC board update
    [EPC2304.kicad_pcb, EPC2304.kicad_sch, PhaseMosfets.kicad_sch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]
2024-05-29 v3.3.2 - ECP2304 changes
    [ATTinyComp.kicad_sch, Connectors.kicad_sch, DevKit.kicad_pcb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]
2024-05-29 v3.3.2 - EPC readme updated and schematic revised
    [EPC2304.kicad_pcb, PhaseMosfets.kicad_sch]
2024-06-21 v3.3.3 - EPC pcb revised
    [ACS37030LLZATR-040B3.stp, EPC2304.kicad_pcb, EPC2304.kicad_sch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]
